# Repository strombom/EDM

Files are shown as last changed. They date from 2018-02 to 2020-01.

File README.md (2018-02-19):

# EDM

## Control board
* Stepper motor output.
* Power board control output.
* Buttons for stepper motor up/down and EDM start/stop.
* LCD display 4x20 characters for status.
* Potentiometers for setting voltage, current (not implemented in this revision), on-time and off-time.

## Power board
* Voltage source, low current for initiating spark. Selectable 250 V, 200 V, 150 V or 100 V. Status comparator checks if voltage is above 70 V.
* Current source, for providing current to the spark. Current limited to 10 A, adjustable with potentiometer.
Spark output, has two power transistors to enable the control board to control the voltage and current outputs independently. Has two comparators (5 V and 30 V) to give feedback to the control board, monitoring if a spark has started (breakdown) and to check for short circuit.

## Design files
* [Control Board Schematics](https://github.com/strombom/EDM/raw/master/hardware/edm_control_board/documents/edm_control_board_schematics.pdf)
* [Power Board Schematics](https://github.com/strombom/EDM/raw/master/hardware/edm_power_board/documents/edm_power_board_schematics.pdf)

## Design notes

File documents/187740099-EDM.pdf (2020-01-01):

Anand Pandey et. al. / International Journal of Engineering Science and Technology Vol. 2(6), 2010, 2172-2191

# Current research trends in variants of Electrical Discharge Machining: A review

Anand Pandey¹
Assistant Professor, Department of Mechanical Engineering, Anand Engineering College, Agra –India Email: pandeyanand223@gmail.com

Shankar Singh²
Associate Professor, Department of Mechanical Engineering, SLIET (Deemed-to-be-University), Longowal-India Email:singh.shankar@gmail.com

Abstract

Present manufacturing industries are facing challenges from these advanced materials viz. super alloys, ceramics, and composites, that are hard and difficult to machine, requiring high precision, surface quality which increases machining cost. To meet these challenges, non-conventional machining processes are being employed to achieve higher metal removal rate, better surface finish and greater dimensional accuracy, with less tool wear. Electric Discharge Machining (EDM), a non-conventional process, has a wide applications in automotive, defense, aerospace and micro systems industries plays an excellent role in the development of least cost products with more reliable quality assurance. Die sinking EDM, Rotating pin electrode (RPE), Wire electrical discharge machining (WEDM), Micro- EDM, Dry EDM, Rotary disk electrode electrical discharge machining (RDE-EDM) are some of the variants methods of EDM.
The present paper review the state of the art technology of high-performance machining of advanced materials using Die Sinking EDM, WEDM, Micro-EDM, Dry EDM AND RDE-EDM. The review relies on notable academic publications and recent conference proceedings.

Keywords: EDM; RDE-EDM, RPE; WEDM, Micro-EDM

### 1. Introduction

The advanced materials have attractive properties i.e., high strength, high bending stiffness, good damping capacity, low thermal expansion, better fatigue characteristics which make them potential material for modern day industrial application. Present manufacturing industries are facing challenges from these advanced materials viz. super alloys, ceramics, and composites, that are hard and difficult to machine, requiring high precision, surface quality which increases machining cost [1]. To meet these challenges new processes with advanced methodology and tooling needs to be developed. The conventional machining of such advanced materials are often difficult due to the improved thermal, chemical and mechanical properties of new advanced materials. Conventional machining such as turning, milling and drilling etc shows ineffectiveness in machining of advanced materials, since it results in poor materials removal rate, excessive tool wear and increased surface roughness. Non-Conventional Machining processes are classified according to the type of energy used for the machining of the work materials. i.e. Mechanical (Ultrasonic machining(USM), Water jet machining(WJM),Abrasive jet machining (AJM), Thermal Electrical discharge machining(EDM),Electron beam machining(EBM),Laser beam machining(LBM), and Chemical (Chemical machining(CHM),Photo chemical machining(PCM) [2]. The Electric Discharge Machining (EDM), a thermal material removal process, has firmly established its use in the production of forming tools, dies, molds and effectively machining of advanced materials.

ISSN: 0975-5462 | 2172

### 1.1 Overview of EDM

In Electrical Discharge Machining the electrode is moved downward toward the work material until the spark gap (the nearest distance between both electrodes) small enough so that the impressed voltage is great enough to ionize the dielectric [3]. Short duration discharges (measured in microseconds) are generated in a liquid dielectric gap, which separates tool and work piece. The material in the form of debris is removed with the erosive effect of the electrical discharges from tool and work piece [4]. EDM does not make direct contact between the electrode and the work piece where it can eliminate mechanical stresses chatter and vibration problems during machining [5].

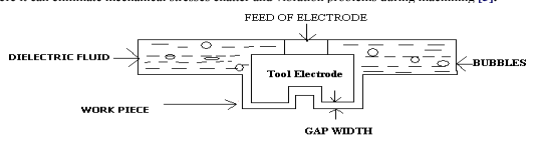
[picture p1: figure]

Fig.1.0 Schematic diagram of EDM

EDM is a non-traditional process based on removing unwanted material in the form of debris from a part by means of a series of recurring electrical discharges (created by electric pulse generators in micro seconds) between a tool called electrode and the work material in the presence of a dielectric fluid( kerosene, distilled water) . The history of EDM begins in 1943, with the invention of its principle by Russian scientists Boris and Natalya Lazarenko in Moscow. They were assigned by the Soviet government to investigate the wear caused by sparking between tungsten electrical contacts, a problem which was particularly critical for maintenance of automotive engines during the Second World War. Putting the electrodes in oil, researchers found that the sparks were more uniform and predictable than in air. They had then the idea to reverse the phenomenon, and to use controlled sparking as an erosion method [6].Lazarenkos developed during the war the first EDM machines, which were very useful to erode hard metals such as tungsten or tungsten carbide. In the 1950’s, progress was made on understanding the erosion phenomenon [7-9]. It is also during this period that industries produced the first EDM machines. Due to the poor quality of electronic components, the performances of the machines were limited at this time. In the 1960’s, the development of the semi-conductor industry permitted considerable improvements in EDM machines. Die-sinking machines became reliable and produced surfaces with controlled quality, whereas wire-cutting machines were still at their very beginning. During the following decades, efforts were principally made in generator design, process automatization, servo-control and robotics. Applications in micro-machining became also of interest during the 1980’s [10]. It is also from this period that the world market of EDM began to increase strongly, and that specific applied EDM research took over basic EDM research [11]. Finally, new methods for EDM process control arose in the 1990’s by using fuzzy control, neural networks response surface methodology, Taguchi optimization.etc.

### 2. Electrical Discharge Machining (EDM)

This section provides the basic fundamentals of the EDM Process and the variations of process combining other material removal methods:

### 2.1 EDM: How it works

The material erosion mechanism primarily makes use of electrical energy and turns it into thermal energy through a series of discrete electrical discharges occurring between the electrode and work piece immersed in a dielectric liquid medium [12]. The thermal energy generates a channel of plasma between the cathode and anode [13] at a temperature in the range of 8000 to 12,000 °C [14]. When the pulsating direct current supply occurring at the rate of approximately 15,000–30,000 Hz [15] is turned off, the plasma channel breaks down. This causes a sudden reduction in the temperature allowing the circulating dielectric fluid to implore the plasma channel and flush the molten material from the pole surfaces in the form of microscopic debris.

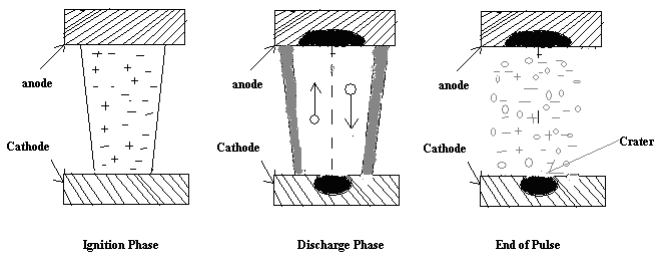
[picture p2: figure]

Fig.2.0 The phases of EDM (Konig and klocke, 1997)

Mc Geough [16] describes the variation of voltage pulses causing the electrical breakdown of the dielectric fluid. A high voltage current is needed to discharge in order to overcome the dielectric breakdown strength of the small gap. The breakdown of this plasma channel occurs because of the acceleration of electrons towards the anode. Electrons impacts with the neutral atoms and molecule of dielectric fluid, thus creating more positive ions and electrons, which accelerated towards the cathode and anode. The impact of these electrons and positive ions to the anode and cathode produces heat energy.
Electrical Discharge occurs at higher frequencies since the metal removal rate for each discharge is very less in change in weight. For every pulse, electrical discharge occurs at a particular position where the electrode materials are melted and evaporated and finally ejected in the molten phase (in the form of debris) thus forming small crater on both tool electrode and work piece. The unwanted material is then cooled and re-solidified in the dielectric fluid forming large number of debris particles which will be flushed away from the gap by the flow of dielectric pressure. During each end of the discharge duration, the temperature of the plasma channel and the electrode surfaces that is in contact of the plasma rapidly drops, resulting in the recombination of ions and electrons. For maintaining stability in EDM process, every successive next pulse discharge occurs at a spot distanced sufficiently far from the previous discharge position. The pulse interval (known as off time period) for the next discharge pulse should be not so much long and not too short .If it is long then the plasma channel that is generated by the previous discharge can be fully de-ionized and the dielectric breakdown strength around the previous discharge location can be recovered by the time the next voltage charge is applied and short pulse interval time produces more surface roughness and instability in machining [17].

### 2.2 EDM Equipments

Electrical discharge machining unit consist of following components:
2.2.1 EDM Circuits

EDM Circuits helps to convert electrical energy into thermal energy and maintain the machining gap (known as spark gap) to generate succession of uniform electrical discharges in the form of sparks. A capacitor is used in the circuits to store electrical energy before discharging each sparks [18].In EDM the most commonly used power supply circuits in EDM process are Resistance –Capacitance (R-C) Circuit, Rotary Impulse Generator Circuit and Controlled Pulse Circuit. RC types of generators are simple and low in cost. It uses resistance and a condenser to generate a nearly a saw tooth voltage waveform. In R-C circuit the condenser of capacitance c is charged through a resistance Rc from a source of current of potential and the charging is continued until the potential of the condenser reaches the breakdown voltage Vc of the gap between the tool and the workpiece.The gap is filled with dielectric fluid. The spark discharge is initiated causing an oscillatory flow of current which reaches a maximum value shortly after the breakdown of the dielectric [19]. Rotary-impulse generator circuit is simply a motor generator set. This type of generator supplies high voltage in excess of 110v. Arcing is frequent since the voltage waveform is uncontrollable, so the tool wear rate is high. In pulse circuit , vacuum tubes or transistors are used to achieve the pulsing switch effect.Resistence can also be provided in these circuits to slow down the time required for charging the capacitor.

2.2.2 Dielectric Unit:

The dielectric unit systems consist of dielectric tank, a pumping unit and a filtering unit to handle types of dielectric. Dielectric is often used when considering the effect of alternating electric fields on the substance. Mineral oil, kerosene and deionized water are generally used as a dielectric fluid in EDM .The Sinker EDM process uses dielectric acts as a medium through which controlled electrical discharge occours.This dielectric also acts as a quenching medium to cool and solidify the gaseous EDM debris resulting from the discharge [20].

2.2.3 Servo feed control:

Servo head is incorporated in EDM to maintain gap voltage since the dielectric parameters constantly fluctuate. Servo mechanism affecting the movement of the electrode may be either electric motor driven, solenoid operated or hydraulically operated or a combination of these. The servo feed control maintain the working gap at proper width [21].

### 2.3 EDM Process Parameters

This section discusses the process parameters of EDM. This section focuses on the effects of process parameters such as electrical and non-electrical parameters on the various performance measures.

2.3.1 Electrical Parameters

- Pulse Duration (Ton): It is the duration of time measured in micro seconds. During this time period the current is allowed to through the electrode towards the work material within a short gap known as spark gap. Metal removal is directly proportional to the amount of energy applied during the on time period [22]. Pulse duration is also known as pulse on time and the sparks are generated at certain frequency. Material removal rate depends on longer or shorter pulse on time period. Longer pulse duration improves removal rate of debris from the machined area which also effects on the wear behavior of electrode. As in EDM process erosion takes place in the form of melting and vaporization of both the tool and work material at the same time period, so with longer pulse duration more material has to be melt and vaporize. The resulting crater produced will be broader as comparison to the shorter pulse on time. But, in some experimental research work it has been proved that optimal pulse duration gives higher performance measures [23]. It conclude all that MRR can not be increased by increasing the Pulse on time, a suitable combination of peak current is also needed for increasing rate of removing unwanted material from the work piece. At constant current and constant duty factor, the MRR is decreased with increase in pulse on time [24]. This is due to the reason because of short pulses cause less vaporization, where as long pulse duration causes the plasma channel to expand rapidly. This expansion of plasma channel cause less energy density on the work material, which is not sufficient to melt and vaporize the work material. It was also concluded by the researchers that with increase of pulse duration, surface roughness decreased, hardness of work material, crack length, crack width and the thickness of recast layer increased.

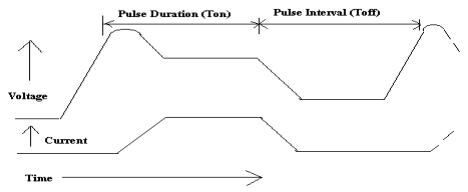
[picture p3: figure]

Fig.3.0 Actual profile of single EDM pulse (Fuller, 1996)

- Pulse Interval (Toff):

It is the waiting interval time period during two pulses on time periods. In fig.1.7, it is the duration of time in which no machining takes place (idle time period) and it allows the melt material to vaporize and to remove from setting. This parameter is to affect the speed and the stability of the cut. If the off-time is too short, it improves MRR but it will because more sparks to be unstable in the machining zone .Kansal et al.
[25] result out that increase in pulse interval time decreases the MRR. Saha et al. [26] reported out that for small value of pulse interval time period, the MRR was low, but with further increase MRR increases. MRR was dropped slowly with increase in pulse interval time. This is due to very short pulse interval the probability of arcing is larger because dielectric in the gap does not recover its dielectric strength. O.A. Abu Zeid investigated the role of voltage, pulse off time in the electro discharge machined AISI T1 high speed steel [27]. The researcher concluded that the MRR is not so much sensitive to pulse interval time changes at low pulse on time in finish machining.

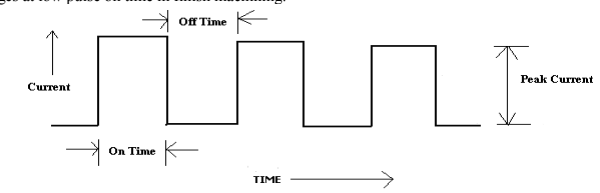
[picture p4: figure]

Fig.4.0 Pulse wave form of pulse generator [28]
- Electrode gap (spark gap):
It is the distance between the electrode and the part during the process of EDM. An electro-mechanical and hydraulic systems are used to respond to average gap voltage. To obtain good performance and gap stability a suitable gap should be maintained. For the reaction speed, it must obtain a high speed so that it can respond to short circuits or even open gap circuits. Gap width is not measured directly, but can be inferred from the average gap voltage [28].

### 2.3.2 EDM Research

Electrical discharge machining is one of the profitable machining processes used for accurate and high precision geometry of the work piece. EDM can become more reliable by doing the research on performances to be obtained by it. Some of the research areas in EDM are shown in fig.5.0

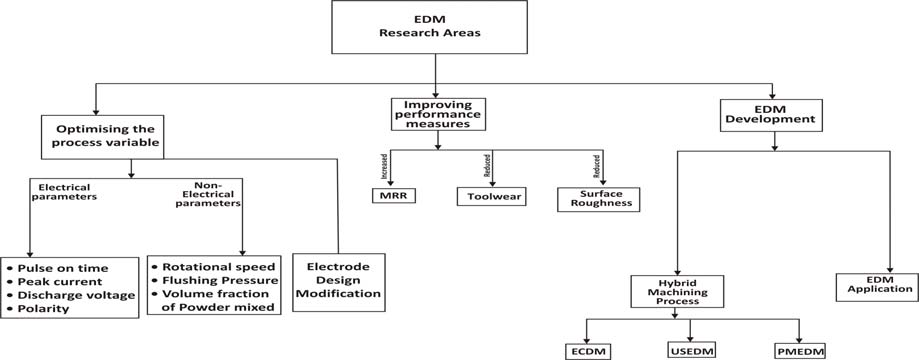
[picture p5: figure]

Fig.5.0 Classification of EDM research

- Duty cycle:
It is a percentage of the on-time relative to the total cycle time. This parameter is calculated by dividing the on-time by the total cycle time (on-time plus off-time).It indicates the degree of efficiency of the operation.

F.L.Amarim result out the effect of duty cycle on the machining of AMP-8000. The researchers concluded that increase of duty factor increases MRR. This is due to the reason that with increase of duty cycle a black layer was seen on the surface of work material and with further more increase of it, the machining becomes unstable [29].MRR increases with increase in duty factor at constant current constant pulse on time [24].This is due to the reason that with increase in duty cycle, the intensity of spark increases resulting in higher MRR.

- Polarity:
It may be positive or negative connected to tool electrode or work material. Polarity can affect processing speed, finish, wear and stability of the EDM operation. It has been proved that MRR is more when the tool electrodes are connected at positive polarity(+) than at negative terminal( -) .This may be due to transfer of energy during the charging process is more in this condition of machining. When a electrical discharge is generated electrons dispatch from the negative polarity collides with neutral molecules between the work piece and electrode which is responsible for ionization process in EDM. However, ionization is taken because the electron arrives at the positive terminal of the surface. The negative polarity is more desirable as compared to positive polarity [30]. The researcher concluded this is because the MRR is higher and better surface finish is produced as MRR is dependent on anode potential drop. Chow et al. experimentally work on the micro slitting on titanium alloy with copper as rotating disk as a electrode. They concluded that MRR was lower with positive polarity of work piece as compared to negative polarity. This is due to the fact that with positive polarity of work piece, the dissociated carbon elements in the dielectric fluid tend to adhere to the anode, which result in forming a recast layer [31].

### 2.4. Non Electrical Parameters

Non-electrical parameters such as the Rotational movement of electrode, flushing of dielectric fluid and aspect ratio ( tool shape) together play a significant role in delivering optimal performance measures. This section discusses the effects of non-electrical parameters on the various performance measures.

2.4.1 Rotation of Tool Electrode:

It is the rotational effect of cylindrical (pin shaped) or disc shaped electrode tool measured in revolution/minute. The rotational movement of electrode is normal to the work surface and with increasing the speed, a centrifugal force is generated causes more debris to remove faster from the machining zone. According to Mohan et al. [23], the centrifugal force generated throws a layer of dielectric in to the machining gap, induces an atmosphere for better surface finish, prevent arching and improves MRR. Soni and Chakraverti [32] compared the various performance measures of rotating electrode with the stationary electrode. The results concluded an improvement in MRR due to the better flushing action and sparking efficiency with little tool wear but the surface finish was improved.

2.4.2 Injection flushing:

Flushing removes eroded particles from the gap for efficient cutting and improved surface finish of machined material. Flushing also enables fresh dielectric oil flow into the gap and cools both the electrode and the work piece. Basic characteristics required for dielectric used in EDM are high dielectric strength and quick recovery after breakdown [33].There variations of EDM processes can be classified according to the type of dielectric fluid used. Most dielectric media are hydrocarbon compounds and water. The hydrocarbon compounds are in the form of refined oil; better known as kerosene. While the fluid properties are essential, the correct fluid circulating methodology is also important. The dielectric fluid not only forms a dielectric barrier for the spark between the work piece and the electrode but also cools the eroded particles between the work piece and the electrode. The pressurized fluid flushes out the eroded gap particles and remove the debris from the fluid medium by causing the fluid to pass through a filter system [34].During the investigation of EDM of Ti 6Al 4V, Chen et al. [35] found that the MRR was greater and the relative EWR is lower, when using 16 distilled water as dielectric solution.

2.4.3 Tool Geometry:

Tool geometry is concerned with the shape of the tool electrodes.ie. Square, rectangle, cylindrical, circular.etc. The ratio of length /diameter of any shaped feature of material. In case of rotating disk electrode the ratio becomes thickness/diameter. Murali et al [36] used graphite foil for straight grooving operation instead of pin shaped electrode. An aspect ratio of 2.3 was achieved by using FAST technique (Foil as tool electrode) which was improved to 8 by implementing GAME (Gravity assisted Micro EDM). Singh et al. [37] uses square and rectangular shaped electrodes having aspect ratio of 1.0 and 0.6 for machining 6061Al/Al2O3P composite .It concluded that shape of the electrode effects EWR. The tool having less aspect ratio gave higher value of EWR.Thus with increasing the size of electrode more good performance of ED Machining takes place.

2.4.4 Tool Material (Electrode):

Engineering materials having higher thermal conductivity and melting point are used as a tool material for EDM process of machining . Copper, graphite, copper-tungsten, silver tungsten, copper graphite and brass are used as a tool material (electrode) in EDM. They all have good wear characteristics, better conductivity, and better sparking conditions for machining. Copper with 5% tellurium, added for better machining properties. Tungsten resist wear better than copper and brass .Brass ensures stable sparking conditions and is normally used for specialized applications such as drilling of small holes where the high electrode wear is acceptable (Metals Handbook, 1989). The factors that effect selection of electrode material include metal removal rate, wear resistance, desired surface finish, cost of electrode material manufacture and material and characteristics of work material to be machined.

### 2.5 Recast Layer in EDM:

In EDM process as the sparks are generated the material begins to melt and vaporize with small crater, thus reducing the area of work piece material into gas bubbles. During the each cycle period EDMed crater gets larger, its increasing surface area begins to sink heat away from the spark gap until the vaporization temperature can no longer be sustained. The melting process continue but an pulse interval time period is required to flush away the eroded material .During the off time period when the current is switched off, melting ceases instantly and all molten material break away in the form of small spherical bubbles is drawn back by the surface tension and resolidifies back on to the cooler layer of cut material. This thin layer of resolidified material is called recast layer or white layer [38]. Immediately below the recast layer is the area termed as heat affected zone (HAZ). This area is partially affected by the elevated temperature of the spark gap. Within this area, the material did not approach temperature large to melt, but reaches a temperature high to change its temper, reducing its hardness. While machining the maraging steel with EDM process a recast layer was formed [24]. These results in premature part failure and shorten the life of part’s fine surface finish.

Fig.6.0 EDM heat effected Zones [41]

Pandey et al. [39] reported out that the thickness of the recast layer formed on the work piece and the level of
thermal damage | suffered | by the electrode can be determined by analyzing the growth of the plasma
channel during sparking. The EDM generates heat affected zone in the machining zone [40]. The researchers measured the micro hardness around the micro- EDMed hole crossections. They concluded that HAZ in micro EDM comprises of low hardness instead of white layer.

### 3.0 EDM Variants

In die sinking process the tool electrode is the replica of the machined profile of the work material shown in fig 7.0 Die sinking process solves the problem of manufacturing accurate and complex-shaped electrodes of three-dimensional cavities. According to the article “Advancing EDM through Fundamental Insight into the Process” by M. Kunieda Tokyo University of Agriculture and Technology, Japan), B. Lauwers (Katholieke Universities Leuven, Belgium), K.P. Rajukar (University of Nebraska-Lincoln, USA), B.M Schumacher (University of Applied Science St Gallen, Switzerland),the work piece can be formed either by replication of a shaped tool electrode or by 3-Dimensional movement of a simple electrode similar to milling or we can use the combination of both the methods.

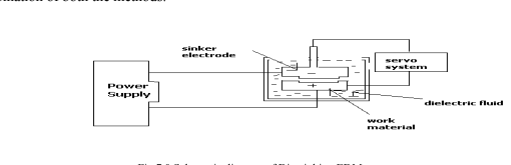
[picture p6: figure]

Fig.7.0 Schematic diagram of Die-sinking EDM
A number of EDM variations based on this basic configuration have emerged in the industry to cope with the machining of smart materials or super alloys used exclusively in the manufacture of aeronautical and aerospace parts. Wire-cut EDM (WEDM) and Rotary Disk electrode electrical discharge machining process (RDE-EDM) are some of the most favorable variants owing to its ability to machine conductive, exotic and high strength and temperature resistive (HSTR) materials with the scope of generating intricate shapes and profiles [41].

### 3.1 Wire EDM process:

WEDM was first introduced to the manufacturing industry in the late 1960s. In WEDM, material is eroded from the work material by a series of discrete sparks occurring between the work piece and the wire separated by a stream of dielectric fluid, which is continuously fed to the machining zone [42]. The WEDM process makes use of electrical energy generating a channel of plasma between the cathode and anode [43], and turns it into thermal energy at a temperature in the range of 8000–12,000 ºC [44]. When the pulsating direct current power supply occurring between 20,000 and 30,000 Hz [45] is turned off, the plasma channel breaks down. This causes a sudden reduction in the temperature allowing the circulating dielectric fluid to implore the plasma channel and flush the molten particles from the pole surfaces in the form of microscopic debris.

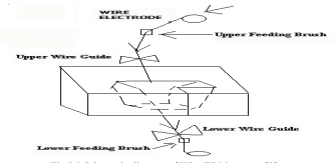
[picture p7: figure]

Fig.8.0 Schematic diagram of Wire EDM process [2]

3.1.1 WEDM process monitoring and control of smart material

Lok et al. [46] presented the finding of processing two advanced materials Sialon and Al2O3-TiC by using WEDM. The author has taken MRR and surface finish as output parameters. The surface damage was evaluated by flexural strength data. The variability of flexural strength data was analyzed by weibull stastical method. The mean flexural strength drops from 32% to 67% due to thermal spalling erosion mechanism of wire-cut EDM process. Yan et al. [47] machined aluminum matrix composites (Al2O3p/6061 Al) using WEDM. The effect of pulse on time, cutting speed, width of slit, surface roughness was studied. The wire easily got broken while machining Al2O3p/6061 Al. It was observed that that the cutting speed, surface roughness and width of the slit significantly depend upon volume fraction of Al2O3 particles. Less volume percentage of reinforcement increases the surface finish, improves width of slit.
Hascaly et al. [48] performed an experiment for finding out the machining characteristics of AISI D5 tool steel in WEDM. The author concluded that intensity of process energy affect the surface roughness as well as micro cracking. The wire speed and fluid pressure do not have much influence. Gokler et al. [49] performed experiments to optimize the cutting and offset parameter combination for WEDM process to achieve the desired surface roughness. The author has performed experiments on 1040 steel material of thickness 30, 60 and 80 mm and on 2379 and 2378 steel materials of thickness 30 and 60 mm. It was concluded that increase in the work piece thickness creates better surface roughness characteristic.Tarng et al. [50] used a neural network system to determine settings of pulse duration, pulse interval, peak current, open circuit voltage, servo reference voltage, electric capacitance, and table speed for the estimation of cutting speed and surface finish.

3.1.2 Wire breakage in EDM

A wide variety of the control strategies preventing the wire from breaking are built on the knowledge of the characteristics of wire breakage .Saha et al. [51] developed a model that predicts the thermal distribution accurately, increase wire velocity and reduction in heat transfer coefficient. He has found that non uniform heating is the most important variable affecting the temperature stress. FE Model would help to prevent wire breakage. Tosun et al. [52] found that increasing pulse duration and open circuit voltage increase the wire wear rate, whereas the increasing wire speed and dielectric fluid pressure decreases the wire wear. Luo et al. [53] claimed that the wire material yielding and fracture contribute to the wire breakage, whilst an increase in temperature aggravates the failure process.

3.1.3 Modeling of WEDM process

Tarng et al. [50] formulated a neural network model and simulated annealing algorithm in order to predict and optimize the surface roughness and cutting velocity of the WEDM process when machining of SUS-304 stainless steel materials. T.A. Spedding and Z.Q.Wang [54] attempted to model the cutting speed and surface roughness of WEDM process through the response-surface methodology and artificial neural networks (ANNs) and have found that the model accuracy of both the approaches were better. The same authors (T.A. Spedding and Z.G. Wang, 1997) attempted further to optimize the surface roughness, surface waviness and speed of the artificial neural networks that predicted values using a constrained optimization model. Lin et al. [55] proposed a control strategy based on fuzzy logic to improve the machining accuracy. Huang and Liao [56] presented the use of Grey relational and S/N ratio analyses, for determining the optimal parameters setting of WEDM process. The results showed that the MRR and surface roughness are easily influenced by the table feed rate and pulse on time.

### 3.2 MICRO EDM

According to CIRP committee of Physical and Chemical processes, the term micro-machining defines the processes that manufacture products in the range of 1 to 999 μm [57]. Initially, the term was used to present the miniaturization of electronic components and devices. However, with the present trend in the miniaturization of mechanical components, it is also being applied for the generation of microscopic mechanical components and devices[28].In order to reduce the size of product micro-edm was developed and the basic physical characteristics of the micro-EDM process is essentially similar to that of the conventional EDM process with the main difference being in the size of the tool(electrode) used, the power supply of current and voltage supply , and the resolution of the X-, Y- and Z- axes movement. The system has a servo system with highest sensitivity and positional accuracy of + 0.5 μm [58].It permits setting of a minimized discharge gap width of 1 μm [59]. There fore, the system is helpful for conventional precision engineering purposes as well as for micro-components fabrication like micro-molds, micro inserts, and in general filigree structure up to 5 μm [58].
Yan et al. [60] investigated effects of various machining parameters on the quality of the micro-hole machining of carbide by EDM. Fuel injector valves, parts and components for medical devices, fiber optic connectors, micromachining, micro-mold making, stamping tools, and micro electronic parts are the examples of miniaturized and smaller size parts produced by the micro-EDM technology. . Zhang et al. [61] made an experiment in hole machining of Al2O3 ceramics with small diameter and metal bond diamond wheels after micro electric discharge truing to investigate its effectiveness.
Wansheng et al. [62] demonstrated that holes with diameter less than 0.2 mm and the aspect ratio more than 15 can be produced without difficulty by ultrasonic vibration using micro-EDM .Kaminski and Capuano [63] reported that they studied parameters affecting the micro-hole machining process with diameters smaller than 0.1 mm and aspect ratio bigger than 20 by electro erosion penetration process in sheets. Diver et al. [64] investigated the possibility of a novel technique to produce reverse tapered micro-holes using EDM. High quality reverse tapered holes are claimed to be produced, showing excellent hole form, with hole diameter variation around 3 μm and cycle times similar to standard EDM for straight holes. The quality of hole surface finish maintained at Ra=0.3 μm. Liu et al. [65] investigated the feasibility of fabricating high nickel alloy using micro-EDM, and micro-holes were successfully fabricated in high nickel alloy. Liu et al. [66] studied micro-EDM combined with High-Frequency Dither Grinding (HFDG) to improve the surface roughness of micro-holes, reducing from 2.12 μm to 0.85 μm without micro cracks.

### 3.3 DRY EDM:

Dry EDM uses gas-liquid mixture as the two phase dielectric fluid and has the advantage the concentration of liquid and properties of dielectric fluid to meet desired performance responses. In dry EDM, tool electrode is formed to be thin walled pipe. Dry EDM uses gas as dielectric fluid, and high MRR can be obtained to cut high strength engineering materials with the presence of oxygen [67–70].High-pressure gas or air is supplied through the pipe. The role of the gas is to remove the debris from the gap and to cool the inter electrode gap. The technique was developed to decrease the pollution caused by the use of liquid dielectric which leads to production of vapour during machining and the cost to manage the waste. V.Ramani et al. [71] reported that helium and argon can be used as a dielectric medium to drill holes using copper electrodes. Later on Kunieda et al. [72] confirm that by introducing oxygen gas into the discharge gap increases the material removal rate in water as a dielectric medium. Tao et al. [73] concluded that by combining oxygen gas with copper tool gives high MRR in dry EDM. Dry EDM with air as the dielectric is feasible with reverse polarity [26].

### 3.4 Rotating Disk Electrode(RDE)-EDM:

Machining by using Rotary Disk Electrode is a typical method of EDM, which develops in recent years. In recent years the studying of micro electro mechanical Systems (MEMS) have resulted in the manufacture of small size products such as micro-pumps, micro-engines and micro-robots that have been successfully used in industrial applications. The technique of precision machining for such small devices has become increasingly important [74–77]. Rotary disc electrode electrical discharge machining is one of the variant process of electrical discharge machining process based on removing unwanted material in the form of debris from a part by means of a series of recurring electrical discharges (created by electric pulse generators in micro seconds)between a rotary tool called disc( thickness ranging from micron level to 1 mm) and the work material in the presence of a dielectric fluid( kerosene, distilled water ). This fluid makes it possible to flush eroded particles from the gap.
This new application of RDE-EDM machining is achieved by locating the rotating disk Electrode above or below the work piece to improve the debris removal rate.

### 3.4.1 Past work done on RDE-EDM:

A significant number of papers have been reviewed on ways of yielding optimal performance measures of high MRR, low tool wear rate (TWR) and satisfactory surface quality. This section will review all the past research work done in rotary EDM for machining advanced materials.
Several researchers have explained the material removal mechanism in terms of migration of material elements between the rotary disk electrode (RDE) and work piece. The material removal takes place not only by vapour ejection but also due to liquid expulsion. Sato et al. [78] developed an electrical discharge machine for micro-hole boring. They claimed that electrode rotation served as an effective gap flushing technique, yielding better material removal.
Soni & Chakraverti [32] introduced rotary disc for grooving operation on titanium alloy. The rotary electrode was placed above the work material. The difficulty of debris problem was encountered the research work i.e. lower metal removal rate and arching occurs due to the accumulation of debris particle between the electrode and work piece.
Soni et al. [79] experimented the machining of die steel and titanium alloy with a rotary and low vibrating copper-tungsten electrode revealed that electrode rotation improves the material removal rate. They also studied the alloying effect of migrating material from electrode and work material. During the research it was observed that performance measures between rotary and stationary electrodes revealed improvement in material removal due to better flushing action and sparking efficiency with low electrode wear during rotary electrical discharge machining. Soni et al. [80] uses copper-tungsten electrode for blind and through hole operation on high carbon high chromium die steel and titanium alloy. It was found that metal removal rate was increased due to rotating electrode which increases the flushing action. Material removal rate was more in case of die steel than titanium allow due to its lower specific strength and less hardness.

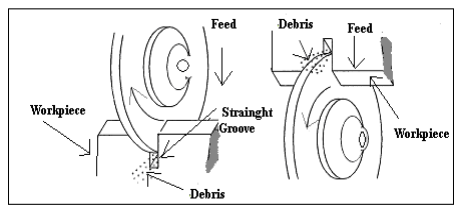
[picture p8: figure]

Fig.9.0 Rotating Disk Electrode Schematic Diagram [81]
Chow et al. [81] used rotary electrode in a modified conventional electrical discharge machine for micro slitting of work piece. The research concluded that increase in material removal and uniform decrease in electrode wear around its periphery by locating the work piece above rotary disk electrode. Reduction in recast layer thickness and lesser micro cracks concentration was also observed on the eroded surface. Yan et al. [82] optimized the cutting of Al2O3/6061Al composite using rotary electrical discharge machining with a disk like electrode with Taguchi methodology. Taguchi methodology revealed that, in general electrical parameters ( Peak Current, Pulse duration and gap voltage) affects the machining characteristics(material removal rate, electrode wear rate & surface roughness) more significantly than the non-electrical parameters (speed of rotational disc).High MRR was found due to superior debris disposal effect of RDE.
C.C.Wang et al. [83] optimizes the blind-hole drilling of Al2O3/6061Al composite using rotary electro-discharging machining by using Taguchi methodology. Increase of rotational speed of the electrode or the injection flushing pressure of the dielectric fluid result in a higher MRR. Ghoreishi and Atkinson [84] compared the effects of high and low frequency forced axial vibration of the electrode rotation in EDM. Vibro-rotary increases less material removal rate as compared with vibration EDM alone but improved surface finish .Combination of ultrasonic vibration and rotation of electrode leads to increase in MRR, TWR AND SR. Mohan et al. [85] studied the effect of machining variables on MRR.EWR AND SR by blind hole drilling through cylindrical rotary electrode (copper) and compared its result from stationary electrode .MRR increases with increase in discharge current and for specific current it decreases with increases in pulse duration. MRR decreases with increase in vol. % of Sic but Increases with rotational speed of electrode which results in positive effect with MRR, TWR and better SR than stationary electrode. Mohan et al. [23] studied the effect of machining variables by blind hole drilling through cylindrical tube electrode made of brass, having eccentric hole diameters .MRR increases with increase of discharge currents and MRR, EWR and SR were more with positive polarity of the electrode than at negative.
M.Murali et al. [36] uses a graphite foil for making straight grooves by Foil as tool electrode approach (FAST).The profile made by FAST EDM appears to have a concave shape with raised edges. This was further refined by using the Gravitational assisted micro EDM (GAME) in which work material was placed above the foil electrode for the effective debris removal, which has improved the aspect ratio to about 8.

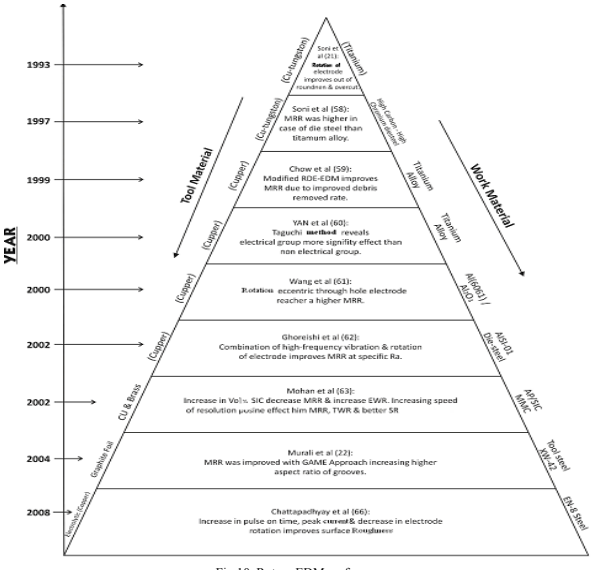
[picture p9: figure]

Fig.10. Rotary EDM performance

Kuo et al. [86] fabricated the micro disk by the application of micro EDM through Wire. The series-pattern micro-disk was used as a rotating tool electrode, which is referred to as micro-rotating disk electrode (MRDE), to simultaneously achieve micro-slits with widths as low as 8 μm. Shih et al. [87] have reported about the electrical discharge grinding of AISI D2 tool steel work piece using a rotary disk copper electrode mounted on horizontal spindle. It was observed that lower electrode wear rate and higher material removal rate can be obtained in this process. Chattopadhyay et al. [88] investigates the machining characteristics of EN-8 steel with copper as a tool electrode during rotary electrical discharge machining process. In the case of MRR and EWR, it has been seen that the decrease in pulse on time, decrease in electrode rotation and increase in peak current, increases both the machining output, while investigation is carried out with rotary electrode.

### 4.0 Hybrid Electrical Discharge Machining Processes

Hybrid machining process in EDM make use of the combined advantages and to reduce some negative effects the combined processes produce better performance as compared to individual process machining. In EDM process the electrical energy is converted to thermal energy, the combined effect of powder suspension and ultrasonic motion of tool or work piece as been reported in this section.

### 4.1 Powder mixed EDM (PMEDM)

EDM process in pure kerosene shows instability resulting to the arcing effect. In order to improve the machining efficiency, the addition of abrasives and metallic powders is done to dielectric fluid. Erden et al. [89] research out the effect of suspended powder particles (Al, Cu, Fe, and carbon) on the mach inability of mild steel. It was observed that the added powder increases the breakdown characteristics of the dielectric fluid, and the machining rate increases with an increase in the concentration of the added powder. It was also observed that the machining becomes Unstable and difficult at an excessive powder concentration due to the occurrence of short-circuiting. Jeswani et al. [90] carried out the research by the addition of fine graphite powder into kerosene oil on the machining of tool steels. It was resulted out that the addition of 4 g/l of graphite powder increases the interspace for electric discharge initiation and lowered the breakdown voltage.

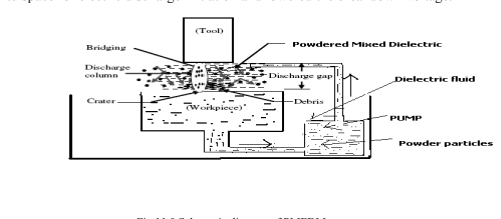
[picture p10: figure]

Fig.11.0 Schematic diagram of PMEDM
Narumiya et al. [91] studied the addition aluminum and graphite powders in dielectric fluid which results in better surface finish than the silicon powder. The best results are obtained for aluminum and graphite powder particles having diameters less than 15 μm and concentration ranges from 2 to 15 g/l. Mohri et al. [92] studied the effect of silicon powder addition into dielectric fluid on the surface finish of H-13 die steel. Machining with addition of silicon powder produces fine and corrosion-resistant surfaces having roughness of 2 μm. Kobayashi et al. [93] investigated the effects of suspended powder in dielectric fluid on surface roughness. It was reported that the surface finish of SKD-61 material is improved with the use of silicon powder. Yan et al. [94] studied the effect of suspended aluminum and silicon carbide powders on EDM of SKD11 and Ti-6Al-4V. Improvement in metal removal rate was observed at the cost of surface finish.
Ming et al. [95] studied out the additives (conductive and inorganic oxide particles) increases the Metal removal rate and decreases the tool wear rate, and improves the surface quality of the work material. Uno et al. [96] investigated the effect of silicon powder mixing on the surface generation mechanism. The EDM with silicon powder mixed fluid produced better surface finish as compared to those produced by EDM with kerosene fluid. It was argued that silicon powder mixed EDM fluid led to smaller undulation of a crater because the impact force acting on the work piece is smaller. This results in the stable machining without a short-circuit between the electrode and the work material. In another study, Uno et al. [97] result out that nickel powder mixed EDM modifies the surface of aluminum bronze components. Nickel powder deposit a layer on an EDM surface to make the surface abrasion-resistant. Wong et al. [98] observed that machining of SKH-54 tool steel in addition of graphite powder particles results in higher material removal rate and better discharge dispersion. Chow et al.
[99] studied the EDM process by adding Sic and aluminum powders into kerosene for the micro- slit machining of titanium alloy. Mixed Sic and aluminum powder to the kerosene enhanced the gap distance, resulting in higher debris removal rate and material removal depth. Pecas et al. [100] result out the effect of silicon powder mixed dielectric on EDM. Improvement in surface finish was assessed through quality surface indicators and process time measurements over a set of different processing areas.

Kansal et al. [101] experimentally studied the effect of addition of silicon powder in dielectric fluid and enhanced rate of material removal and surface finish was achieved. Empirical modelling with response surface methodology concluded the variation of response parameters in terms of independent parameters within the specified range. The silicon powder suspended in the dielectric fluid of EDM affects both MRR and SR. It was found that MRR increases with the increase in the concentration of the silicon powder. Later on Kansal et al.
[25] studied the effect of addition of silicon powder on machining rate of AISI D2 Die Steel. It was found that Peak current, concentration of the silicon powder; pulse-on time, pulse-off time, and gain significantly affect the material removal rate in PMEDM. Chow et al. [102] uses Sic powder in water as dielectric for micro slit operation. They concluded that the addition of Sic powder increases the electrical conductivity, enlarge the inter electrode gap, removes debris easily and increases MRR.Till very few researches has been seen in grooving and slitting machining operation with addition of powder mixed EDM. Kozak et al. [103] have estimated that electrical breakdown in the gap with conducting/non-conducting abrasive powders would be initiated at 3 or 1.5 times larger distance than in case of EDM with pure dielectric fluid, respectively. Extensive studies on the role of abrasives in AEDM have revealed that in hybrid ED process, using abrasive powder, the thermal erosion phenomenon is directly involved in metal removal whereas, the presence of powder assists in improving the machining capabilities by creating a favourable machining environment. Some hybrid processes have also been employed on composites to study their effects. Abrasive powder-mixed EDM or Abrasive EDM (AEDM) was utilised to explore the influences of process parameters. This process requires proper powder suspension and continuous filtration for ensuring even distribution throughout the cavity, facilitating excellent sidewall finishes, thus restricting it to finish machining of component [104].
Later on a comparative machinability study has also been carried out on stir-casted 6061Al/Al2O3p/20p work specimens with copper electrode tools by using plain dielectric fluid and Silicon Carbide (Sic) abrasive powder-suspended dielectric fluid and evaluating the machinability in terms of Surface Roughness (SR). The results of both the processes were analysed using Lenth’s method to find the significant parameters and obtaining optimum machining parameter settings. It was found experimentally that Abrasive Particle Size (APS); Abrasive Particle Concentration (APC) and pulse current are the most significant parameters that affect the
surface characteristics[105]. Singh et al. | analyse the effect of | Abrasive powder-mixed EDM of
6061Al/Al2O3p/20p work specimens with copper tool electrode .They concluded that tool electrode lift time and aspect ratio (shape of the tool electrode) also have considerable effect on the machining performance. Experimental results also indicate that compared with conventional EDM, APM/EDM performance, as regards metal removal rate and surface finish, is much superior. In this study, the MRR in APM/EDM is almost twice that possible with EDM. Similar trend is also noticed for surface finish [106].

### 4.2 Ultrasonic Assisted EDM (USEDM)

The hybrid effect ultrasonic vibration of the electrode with EDM has been undertaken since mid 1980s. Ultrasonic is concerned with the vibratory wave of frequency above 16 Kc/s [107]. Ultrasonic machining combined with Electrical discharge machining can improve material removal rate as high as possible on account of decreasing surface finish. It can be used to machine high strength materials i.e. composites and super alloys. In USEDM process the abrasive slurry is replaced by suitable dielectric fluid (kerosene, distilled water,). The Ultrasonic vibration of tool or work piece in combination with electrical discharges produced by the electrode removes material effectively. The motion of direction of tool is generally normal to the work surface. The vibrating movement of the tool electrode or the work piece improves the slurry circulation and the pumping action, by pushing the debris away and sucking new fresh dielectric and which provides ideal condition for discharges, their efficiency and gives higher removal rate [108].

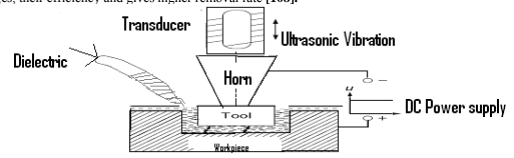
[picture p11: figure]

Fig.12.0 Schematic diagram of USEDM [2]

4.2.1 Tool Vibration in EDM

Murti and Philip (109) added that with the combination of ultrasonic vibration in EDM the MRR and surface finish improved significantly and the tool wear rate increased. Zhixin et al. [110] has produced an ultrasonic vibration pulse electro-discharge machining (UVPEDM) to produce holes in ceramics material. High material removal rate (MRR) was confirmed during the experimental work. Ogawa et al. [111] reported out that the depth of micro holes by the combined effect of EDM with ultrasonic vibration becomes almost two times as that without ultrasonic vibration and machining rate was increased. Yan et al. [112] result out that with combined effect of micro electrical discharge machining (MEDM) and micro ultrasonic vibration machining (MUSM) , the diameter variation between the entrance and exit (DVEE) could obtained about 2 mm in micro holes with diameters of about 150 mm and depth of 500 mm. Ghoreishi and Atkinson [81] compared the effects of high and low frequency forced axial vibration of the electrode, rotation of the electrode and combinations of the methods in respect of MRR, tool wear ratio (TWR) and surface quality in EDM die sinking process. They concluded that vibro-rotary increases MRR by up to 35% compared with vibration EDM and by up to 100% compared with rotary EDM in semi finishing.

4.2.2 Work piece Vibration in EDM

Egashira et al.[113] adopted to vibrate the work piece during machining. Micro holes as small as 5 m in diameter in quartz glass and silicon was machined by EDM with combined effect vibration. In the machining range, high tool wear occurs and sintered diamond tool was used to make machining effective. Prihandana et al.
[114] work out the effect of vibratory work piece. It was result out that work piece vibration increases the flushing effect and high amplitude combined with high frequency increase the MRR. Till less research work has been reported with work piece vibratory motion by EDM process.

### 5.0 Summary

EDM has resulted out as most cost effective and precision machining process in recent years. The capacity of machining hard and difficult to machine parts has made EDM as one of the most important machining processes. The contribution Variants of EDM has brought tremendous improvements in the surface finish of machined advanced engineering materials. Powder mixed EDM and Ultrasonic assisted EDM has not only reduces tool wear but also increases material removal rate. Modeling and optimization of various electrical and non electrical parameters in EDM improved in precision machining of work materials The review of the research trends in EDM on rotary EDM, dry EDM machining, EDM with powder additives, Ultrasonic assisted EDM ,WEDM and Micro EDM performances is presented. In each topic, the development of the methods for the last 50 years is discussed.

References:

1] Kozak, J.; Rajurkar, K.P. (2001): Hybrid machining processes, Evaluation and development, Proceedings of 2nd International Conference on Machining and measurement of sculptured surfaces, Krakow, pp.501-536.

2] Hassan, EI-Hofy. (2005): Advanced Machining Processes, McGraw-Hill, pp. 36-37.

3] Bojorquez, B.; Marloth, R.T.; Es-Said, O.S. (2002): Formation of a crater in the work piece on an electrical discharge machine, Engineering Failure analysis, 9, pp.93–97.

4] Marafona, J.; Chousal, J.A.G. (2005):A finite element model of EDM based on the Joule effect, International Journal of Machine Tools & Manufacture, 46, pp. 1–8.

5] Singh, S.; Maheshwari, S.; Pandey, P.C (2004): Some investigations into the electric discharge machining of hardened tool steel using different electrode materials, Journal of Materials Processing Technology 149, pp. 272–277.

6] Lazarenko, B.R. (1943): About the inversion of metal erosion and methods to fight ravage of electric contacts, WEI-Institute, Moscow in Russian.

7] Germer, L.H.; Haworth, F.E. (1949): Erosion of electrical contacts on make, Journal of Applied physics, 20, 11, pp. 1085– 1109.

8] Cobine, J.D.; Burger, E.E. (1955): Analysis of electrode phenomena in the high-current arc, Journal of Applied Physics, 26, 7, pp.895– 900.

9] Zingerman, A.S. (1956): The effect of thermal conductivity upon the electrical erosion of metals, Souvenir of Physics Technology, pp.11945–1958.

10] Sato, T.; Mizutani, T.; Kawata, K. (1985): Electro-discharge machine for micro hole drilling, National Technical Report, 31, pp. 725– 733.

11] Dauw, D.F.; Van. B. (1995): On the evolution of EDM research, part 2: From fundamental research to applied Research, Proceedings of the 11th International Symposium for Electro Machining (ISEM-11), pp. 133–142.

12] Tsai, H.C.; Yan, B.H.; Huang, F.H (2003):EDM performance of Cr/Cu based composite electrodes, International Journal of Machine Tools & Manufacturing, 43, 3, pp.245–252.

13] Shobert, E.I. (1983): What happens in EDM Electrical Discharge Machining: Tooling, Methods and Applications, Society of Manufacturing Engineers, Dearborn, Michigan, pp.3–4.

14] Boothroyd, G.; Winston, A.K. (1989): Non-conventional machining processes, in Fundamentals of Machining and Machine Tools, Marcel Dekker, Inc, New York, 491.

15] McGeough, J.A. (1988): Electro discharge machining in Advanced Methods of Machining, Chapman & Hall, London, 130.

16] McGeough, J.A. (1988): Advanced Methods of Machining, 1st edition. Chapman and Hall, USA, ISBN 0-412-31970-5.

17] Konig, W.; Klocke, F. (1997): Fertigungsverfahren-3, Abtragen and Generieren, Springer, Berlin.

18] Bawa, H.S. (2004): Manufacturing Process-II, The McGraw Hill Companies, pp.186-187.

19] Shah, A.; Prajapati, V.; Patel, P.; Pandey, A. (2007): Development of Pulsed Power DC Supply for Micro-EDM.

20] Mishra, P.K. (1997): Non Conventional machining, The institution of Engineers-India, pp.106-107.

21] Pandey, P.C.; Shan, H.S. (2003): Modern Machining processes, Tata McGraw Hill, pp.92-93.

22] Singh, S.; Kansal, H.K.; Kumar, P. (2005): Parametric optimization of powder mixed Electrical discharge machining by response surface methodology, Journal of Materials Processing Technology, 169, 3, pp. 427-436.

23] Mohan, B.; Rajadurai, A.; Satyanarayana, K.G. (2004): Electric discharge machining of Al–Sic metal matrix composites using rotary tube electrode”, Journal of Materials Processing Technology, 153–154, pp.978–985.

24] Krishna Mohan Rao, G.; Satyanarayana, S.; Praveen, M.(2008):Influence of machining parameters on electric discharge machining of maraging steels-An experimental investigation, Proceeding of the world congress on Eng., Vol. II.

25] Kansal,H.K.; Singh,S.; Kumar,P.(2007):Effect of Silicon Powder Mixed EDM on Machining Rate of AISI D2 Die Steel, Journal of Manufacturing Processes, Volume9, No.1, pp.13-22.

26] Saha, S.K.; Chaudhary, S.K. (2009): Experimental investigation and empirical modeling of the dry electrical discharge machining process, International Journal of machine tools and manufacturing, vol.49, 297-308.

27] Abu Zied,O.A.(1996): The role of voltage pulse off time in the electro discharge machined AISI T1 high speed steel, Journal of Material process Technology,61,pp.287-291.

28] Crookall, J.R.; Heuvelman, C.J. (1971): Electro-discharge machining-the state of the art”, Annual of the CIRP, 20, pp.113-120.

29] Amorim, F.L.; Weingaertnen, W.L. (2002): Influence of duty factor on the die sinking electrical discharge machining of high-strength aluminum alloy under rough machining, Journal of Braz.soc.Mechanical Sciences, 24,194-199.

30] Lee,S.H.; Li,X.P.(2001):Study of the effect of machining parameters on the machining characteristics in electrical discharge machining of tungsten carbide, Journal of materials processing Technology, 115, pp.344-358.

31] Chow, H.M.; Yan, B.H.; Huang, F.Y. (1999): Micro slit machining using electro-discharge machining with a modified rotary disk electrode (RDE), Journal of Materials Processing Technology, 91, pp. 161–166.

32] Soni,J.S.; Chakraverti,G.(1997):Performance evaluation of rotary EDM by experimental design technique, Defense Science journal, Vol. 47, No.1, pp. 65-73.
33] Wong, Y.S.; Lim, L.C.; Lee, L.C. (1995): Effect of Flushing on Electro Discharge Machined Surface, Journal of Materials Processing Technology’. 48, pp. 299-305.
34] Sommer, C. (2000):Non-traditional machining handbook, First edition, Advance Publishing. Houston.
35] Chen, S.L.; Yan, B.H.; Huang, F.Y. (1999): Influence of kerosene and distilled water as dielectric on electric discharge machining characteristics of Ti 6Al 4V, Journal of Materials Processing Technology, 876, pp. 107-111.
36] Murali, M.; Yeo, S.H. (2004): A novel sparks erosion technique for the fabrication of high aspect ratio micro-grooves, Microsystems Technologies, 10, pp. 628–632.
37] Singh, S.; Maheswari, S.; Pandey, P.C. (2007): Optimization of multiperformance characteristics in electrical discharge machining of Aluminium matrix composites (AMCs) using Taguchi DOE methodology, International Journal of Manufacturing Research, vol.2, No.2, pp.138-163.
38] Guitrau, E. (2008): Recast layer, EDM Today.
39] Pandey, P.C.; Jilani, S.T. (1986): Plasma channel growth and the resolidified layer in EDM, Precision Eng, 8(2), pp.104-110.
40] Thao, O.; Joshi, S.S. (2008): Analysis of heat affected zone in the micro-electro discharge machining, International Journal of Manufacturing Technology and Management, Vol.13, pp.201-213.
41] Hassan, EI-Hofy. (2005): Non tradional and Hybrid machining process, McGraw Hill, pp.158.
42] Puri, A.B.; Bhattacharyya, B. (2003): An analysis and optimization of the geometrical inaccuracy due to wire lag phenomenon in WEDM, International Journal of Machine Tools Manufacturing. 43, 2, pp.151–159.
43] Shobert, E.I. (1983): What happens in EDM, Electrical Discharge Machining: Tooling, Methods and applications, Society of Manufacturing Engineers, Dearbern, Michigan, pp. 3–4.
44] Boothroyd, G.; Winston, A.K. (1989): Non-conventional machining processes, Fundamentals of Machining, Marcel Dekker, Inc, 491. 45] McGeough, J.A. (1988): Electro discharge machining, Advanced Methods of Machining, Chapman & Hall, London, 1988, pp. 130. 46] Lok, Y.K.; Lee, T.C. (1999): Processing of Advanced Ceramics Using the Wire-Cut EDM process, Journal of Materials Processing Technology 63, pp. 839-843.
47] Yan, B.H.; Tsai, H.C.; Huang, F.Y.; Lee, L.C. (2005): Examination of wire electrical discharge machining of Al2O3 p/6061Al composites, International Journal of Machine Tools & Manufacture, 45, pp.251–259.
48] Hascaly,A.; Caydas,U.(2004): Experimental study of wire electrical discharge machining of AISI D5 tool Steel, Journal of Material Processing Technology, 148, pp.362-367.
49] Gokler, M.I.; Ozanozgu, A.M. (2000): Experimental investigation of effects of cutting parameters on surface roughness in the WEDM process, International Journal of Machine Tools and Manufacture 40, pp. 1831-1848.
50] Tarng, Y.S.; Ma, S.C.; Chung, L.K. (1995): Determination of optimal cutting parameters in wire electrical discharge machining, International Journal of Machine Tools Manufacturing, 35, 129, pp.1693–1700.
51] Saha, S.; Pachon, M.; Ghoshal, A.; Schulz, M.J. (2004): Finite Element Modeling and optimization to prevent wire breakage in electro discharge machining, Mechanics Research Communications 31, pp. 451-463.
52] Tosun, N.; Cogun, C. (2003): An investigation on wire wear in WEDM”, Journal of Material Processing Technology 134, pp. 273-278. 53] Luo, Y.F. (1999): Rupture failure and mechanical strength of the electrode wire used in wire EDM, Journal of Material Processing Technology, 94, pp.208–215.
54] Spedding, T.A.; Wang, Z.G. (1997): Parametric optimization and surface characteristic of wire electrical discharge machining process, Precision Engineering 20, pp.5–15.
55] Lin, C.T.; Chung, I.F.; Huang, S.Y. (2001): Improvement of machining accuracy by fuzzy logic at corner parts for wire-EDM, Fuzzy Sets and Systems 122, pp. 499–511.
56] Huang, J.T.; Liao, Y.S. (2003): Application of Grey relational analysis to machining parameter determination of wire electrical discharge machining, International Journal of Production Research 41, pp.1244–1256.
57] Masuzawa, T.; Tonshoff, H.K. (1997):Three-dimensional micromachining by machine tools”, Annuals of the CIRP, 46, 2, pp. 621-628. 58] Koch,O.; Ehrfeld,W.; Michel,F.; Gruber,H.P.(2001): Recent progress in micro-electro discharge machining technology-Part1, Proceeding of the 13th International Symposium for Electro machining ISEM XIII, Bilbao, Spain.
59] Newman, S.T.; Ho, K.H. (2003): The state of the art-Electrical discharge machining, International Journal of Machine Tools and Manufacture, 43(13), pp. 1287-1300.
60] Yan, B.H.; Huang, F.Y.; Chow, H.M.; Tsai, J.Y. (1999): Micro-hole machining of carbide by electric discharge machining, Journal of Materials Processing Technology, 87, pp. 139–145.
61] Zhang, C.; Ohmori, H.; Li, W. (2000): Precision shaping of small diameter wheels using micro electric discharge truing and hole-machining of Al2O3 material, International Journal of Machine Tools & Manufacture, 40, pp. 661–674.
62] Wansherg, Z.; Zhenlog, W.; shichun, D.; Guanxin, C.; Hongyu, W. (2002): Ultrasonic and electric discharge machining to deep and small hole on titanium alloy, Journal of Materials Processing Technology vol.120, and pp.101–106.

63] Kaminski,P.C.; Capuano,M.N.(2003):Micro hole machining by conventional penetration electrical discharge machine, International Journal of Machine Tools & Manufacture, 43, pp. 1143–1149.
64] Diver, Atkinson, J.; Li, J.J.L. (2004): Micro EDM drilling of tapered holes for industrial applications, Journal of Materials Processing Technology, 149, pp. 296–303.
65] Liu, H.S.; Yan, B.H.; F.Y.Huang, F.Y.; Qiu, K.H. (2005): A study on the characterization of high nickel alloy micro-holes using micro-EDM and their application, Journal of Materials Processing Technology, 169, 418–426.
66] Liu, H.S.; Yan, B.H.; Chen, C.L.; Huang, F.Y. (2006): Application of micro-EDM combined with high-frequency dither grinding to micro-hole machining, International Journal of Machine Tools & Manufacture, 46, pp. 80–87.
67] Kunieda, M.; Yoshida, M. (1997): Electrical discharge machining in gas, Annuals of the CIRP 46/1, pp.143– 146.
68] Wang, T.; Kunieda, M. (2003): Dry EDM for finish cut, Key Engineering Materials 259–260, pp.562–566.
69] Kunieda, M.; Miyoshi, Y.; Takaya, T.; Nakajima, N.; Yu, Z.B.; Yoshida, M. (2003): High speed 3D milling by dry EDM, Annuals of the CIRP 52/1, pp. 147–150.
70] Yu,Z.B.; Jun,T.; Kunieda,M.(2004): Dry electrical discharge machining of cemented carbide, Journal of Materials Processing Technology 149/ 1–3, pp. 353–357.
71] Ramani, V.; Cassidenti, M.L. (1985): Inert gas Electrical discharge machining, Nasa Technical brief number NPO 15660.
72] Kunieda,M.; Furuoa,S.; Taniguchi,N.(1991):Improvement of EDM efficiency by supplying oxygen gas into gap,CIRP Annuals, Manufacturing Technology,40,pp.215-218.
73] Tao, J.; Shih, A.J.; Ni, J. (2008): Experimental study of the dry and near dry electrical discharge milling processes, Journal of Manufacturing Science and Engineering, 130.
74] Belhardj, S.; Mimouni, S.; Saidane, A.; Benzohra, M. (2003): Using micro channels to cool microprocessors: a transmission-line matrix study, Micros elects, Journal 34/4, pp.247–253.
75] Park, H.; Pak, J.J.; Son, S.Y.; Lim, G.; Song, I. (2003): Fabrication of a micro channel integrated with inner sensors and the analysis of its laminar flow characteristics, Sensors and Actuators A: Physical, 103/3, pp.317–329.
76] Wu, H.Y.; Cheng, P. (2003): An experimental study of convective heat transfer in silicon micro channels with different surface conditions, International Journal of Heat Mass Transfer, 46/14, pp. 2547–2556.
77] Benavides, G.L.; Bieg, L.F.; Saavedra, M.P.; Bryce, E.A. (2002): High aspect ratio meso-scale parts enabled by wire micro-EDM, Micro system Technology, 8, pp.395–4015.
78] Sato,T.; Mizutani,T.; Yonemouchi,K.; Kawata,K.(1986): The development of an electro discharge machine for micro hole borin, Precision Engineering,8,pp.163–168.
79] Soni, J.S.; Chakraverti, G. (1994): Machining characteristics of titanium with rotary electro-discharge machining. Wear, 171, (1/2), pp.51–58.
80] Soni, J.S.; Chakraverti, G. (1997): Performance evaluation of rotary EDM by experimental design technique, Defense Science journal, Vol. 47, No.1, pp.65-73.
81] Chow, H.M.; Yan, B.H.; Huang, F.Y. (1999): Micro slit machining using electro-discharge machining with a modified rotary disk electrode (RDE), Journal of Materials Processing Technology, 91, pp. 161–166.
82] Yan,B.H.; Wang,C.C.; Liu,W.D.; Huang,F.Y.(2000):Machining Characteristics of Al2O3/6061Al Composite using Rotary EDM with a Disk like Electrode, International Journal of Advance Manufacturing Technology, 16, pp.322–333.
83] Yan, B.H.; Wang, C.C.; Liu, W.D.; Huang, F.Y. (1999): Experimental investigation of the blind-hole drilling of Al2O3/6061Al composite using rotary electro-discharging machining, International Journal of Advance Manufacturing Technology, 1999, 18, pp.372–379.
84] Atkinson,J.; Ghoreishi,A.(2002): Comparative experimental study of machining characteristics in vibratory, rotary and vibro-rotary electro-discharge machining, International Journal of Material processing Technology,120,pp.374-384.
85] Mohan, B.; Rajadurai, A.; Satyanarayana, K.G. (2004): Electric discharge machining of Al–Sic metal matrix composites using rotary tube electrode, Journal of Materials Processing Technology, 153–154, pp.978–985.
86] Kuo,C.L.; Huang,J.D.(2004): Fabrication of series pattern micro disk electrode and its application in machining micro-slit of less than 10 μm, International journal of machine tools and manufacture, 44, pp.545-553.
87] Shih, H.R.; Shu, K.M. (2007): A study of electrical discharge grinding using a rotary disk electrode, International Journal of advance manufacturing technology.
88] Chattopadhyay,K.D.; Verma,S.; Satsangi,P.S.; Sharma,P.S.(2008):Development of empirical model for different process parameters during rotary electrical discharge machining of copper-steel(EN-8) system, Journal of Materials processing technology.
89] Erden, A.; Bilgin,S.(1980): Role of impurities in electric discharge machining, Proceeding of 21st International Machine Tool Design and Research Conference, pp.345-350.
90] Jeswani, M.L. (1981): Effects of the addition of graphite powder to kerosene used as the dielectric fluid in electrical discharge machining. Journal of Wear, Volume 70, pp.133-139.
91] Narumiya,H.; Mohri,N.; Saito,N.; Otake,H.; Tsnekawa,Y.; Takawashi,T.; Kobayashi,K.(1989):EDM by powder suspended working fluid”, Proceeding of 9th ISEM, pp.5-8.

92] Mohri, N.; Saito, N.; Higash, M. (1991): A new process of finish machining on free surface by EDM methods, Annuals of the CIRP, 40, 1, pp.207-210.
93] Kobayashi, K.; Magara, T.; Ozaki, Y.; Yatomi, T.(1992): The present and future Developments of electrical discharge machining, Proceeding of 2nd International Conference on Die and Mould Technology, Singapore, pp.35-47.
94] Yan, B.H.; Chen, S.L. (1993): Effects of dielectric with suspended aluminum powder on EDM, Journal of the Chinese Society of Mechanical Engineers, vol.14, and pp.307-312.
95] Ming, Q.Y.; He, L.Y. (1995): Powder-suspension dielectric fluid for EDM, Journal of Materials Processing Technology, vol.52, pp.44-54.
96] Uno, Y.; Okada, A. (1997): Surface generation mechanism in electrical discharge machining with silicon powder mixed fluid, International Journal of Electro Machining, vol.2, pp.13-18.
97] Uno, Y.; Okada, A.; Hayashi, Y.; Tabuchi, Y. (1988): Surface integrity in EDM of aluminum bronze with nickel powder mixed fluid, Journal of Japanese Society of Electrical Machining Engineers, vol.32, pp. 24-31.
98] Wong, Y.S.; Lim, L.C.; Tee, R.I. (1998): Near mirror finish phenomenon in EDM using powder mixed dielectric, Journal of Materials Processing Technology, Vol.79, pp.30-40.
99] Chow, H.M.; Yan, B.H.; Huang, F.Y.; Hung, J.C. (2000): Study of added powder in kerosene for the micro-slit machining of titanium alloy using electro-discharge machining, Journal of Materials Processing Technology, Vol.101, pp.95-103.
100] Pecas, P.; Henriques, E.A. (2003): Influence of silicon powder mixed dielectric on conventional electrical discharge machining, International Journal of Machine Tools and Manufacture, Vol.43, pp.1465-1471.
101] Kansal, H.K.; Singh, S.; Kumar, P. (2005): Parametric optimization of powder mixed electrical discharge machining by response surface methodology, Journal of Materials Processing Technology, 169, pp.427–436.
102] Chow, H.M.; Yang, L.D.; C.T.Lin, C.T.; Chen, Y.F. (2008): The use of Sic powder in water as dielectric for micro slit EDM machining, Journal of Material Processing Technology, 195, pp.160-170.
103] Kozak ,J.; Rozenek,M.; Dabrowski,L.(2003): Study of electrical discharge machining using powder suspended working media, Proceedings of the Institution Mechanical Engineers Part B, Journal of Engineering Manufacture, Vol. 217, pp.1597–1602. 104]Singh,S.;Maheshwari,S.;Pandey,P.C.(2006):An experimental investigation into abrasive electrical discharge machining (AEDM) of Al2O3particulate reinforced Al-based metal matrix composites, Journal of Mechanical Engineering, Vol. 7, No. 1, pp.13–33.
105] Singh, S.; Maheshwari, S.; Pandey, P.C.; Dey, A.(2008):Effect of Sic Powder Suspended Dielectric Fluid on the Surface Finish of 6061Al/Al2O3P/20p Composites in Electric Discharge Machining, International Journal of Machining and Machinability of Materials (IJMMM) InderScience, 4(2/3), pp. 252-274.
106] Singh,S.; Maheshwari,S.; Dey,A.; Pandey,P.C.(2010): Experimental Results and Analysis for Electrical Discharge Machining (EDM) of Aluminium Metal Matrix Composites with Powder-mixed Dielectric - the Lenth’s Method”, International Journal of Manufacturing Technology & Management (IJMTM), Inderscience, Special issue, Int. J. Manufacturing Technology and Management, Vol. 21, Nos. 1/2.
107] Pandey, P.C.; Shan, H.S (2003): Modern Machining Process, Tata McGraw Hill publishing, pp.7.
108] Kozak, J.; Rajurkar, K.P. (2001): Hybrid machining process evaluation and development, Proceedings of the 2nd International Conference on Machining and Measurement of Sculptured Surfaces, Krakow, pp.501–536.
109] Murti,V.S.; Philip,P.K.(1987): A Comparative Analysis of Machining Characteristics in Ultrasonic Assisted EDM by Response Surface Methodology, International Journal of Product Research, 25, 2, pp.259–272.
110] Zhixin, J. (1995): Study on Mechanical Pulse Electro discharge Machining,” Precision Engineering, 17, 2, pp.89–93.
111] Hitoshi, O.; Teruo, N.; .Iwao, M. (2001): Study of Micro Machining of Metals by EDM with High Frequency Vibration”, Takushima Prefectual Industrial Technology Center.
112] Yan,B.H.; Wang,A.C.; Huang,C.Y.; Huang,F.Y.(2002): Study of precision micro-holes in borosilicate glass using micro EDM combined with micro ultrasonic vibration machining, International Journal of Machine Tools & Manufacture, 42,pp. 1105–1112. 113] Egashira, T. (1999): Micro ultrasonic machining by the application of work piece vibration”, CIRP Annals— Manufacturing Technology, 48, pp. 131–134.
114] Prihandana,G.S.; Hamdi,M.; Wong,Y.S.;Kimiyuki,M.(2006): Effect of vibrated electrode in electrical discharge machining, Proceedings of the First International Conference and Seventh AUN/SEED-Net Field wise Seminar on Manufacturing and Material Processing, Kuala Lumpur, pp. 133–138.

Authors’ Biographies

Anand Pandey is currently Assistant Professor in the Department of Mechanical Engineering at Anand Engineering College-Agra- India. He received his B.E in Industrial & Production Engineering from Guru Ghasidas University, Bilaspur, India in 2002 and his M.Tech in Manufacturing System engineering from Punjab Technical University, Calendar (India) in 2006. Pandey is currently pursuing his Ph.D from S.L.I.E.T (Deemed to be University)-Longowal. He has published more than 12 papers in International & National conference proceedings. His area of research is Conventional & Non conventional machining process & Composite Materials. He is a life member of ISTE (India).

Dr. Shankar Singh is currently Associate Professor at Department of Mechanical Engineering, Sant Longowal Institute of Engineering and Technology (Deemed-to-be-University), Longowal, Dist. Sangrur (Punjab), India. He has been awarded Ph.D in Production Engineering from University of Delhi, Delhi, India in 2007. Earlier, he received his Bachelor in Engineering (Mechanical) Hons. from Aligarh Muslim University, Aligarh (UP) and M. Tech (Production) from Punjab Technical University, Jalandhar (Pb.) in India. His current research interests include Automotive Engg., Non-Conventional Manufacturing Processes such as Electric Discharge Machining (EDM) etc., Hybrid Machining Processes: Abrasive Powder-mixed EDM, Electro-chemical Discharge Machining etc., and Production, Processing, Characterization and Machining of Metal Matrix Composites (MMCs). His name has been included in the Who's Who in the World (9

th
Edition and 25th Anniversary Edition) of ‘Marquis Who's Who in Science and Engineering’ and First Edition of ‘Marquis Who's Who in Asia’. His name also finds place in 'Leading Engineers of the World 2007', published by International Biographical Centre, Cambridge, England. His name has been nominated for inclusion in the ‘2000 Outstanding Scientists 2008/2009’, published in 2009, by International Biographical Centre, Cambridge, England. He has published 45 technical papers in the International Journals and proceedings of International and National conferences.

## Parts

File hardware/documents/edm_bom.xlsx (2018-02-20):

Ref | Qnty | Value | Digikey
BTN1 | 4 | Button black | 401-1152-ND
KNB1 | 4 | Knob black | 1568-1601-ND

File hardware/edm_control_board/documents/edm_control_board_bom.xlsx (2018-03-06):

Ref | Qnty | Value | Digikey | Footprint
C201, C202, C203, C204, C205, C209, C206, C303, C304, C602 | 10 | 100n | 445-1418-1-ND | Capacitor_SMD:C_0805_2012Metric
C207 | 1 | 1u | 587-2910-1-ND | Capacitor_SMD:C_0805_2012Metric
C210, C208 | 2 | 12p | 311-1100-1-ND | Capacitor_SMD:C_0805_2012Metric
C212, C211 | 2 | 2u2 | 311-3425-1-ND | Capacitor_SMD:C_0805_2012Metric
C301, C302 | 2 | 330n | 1276-6813-1-ND | Capacitor_SMD:C_0805_2012Metric
C305, C306, C601 | 3 | 10u | PCE4209CT-ND | Capacitor_SMD:CP_Elec_6.3x5.3
C401 | 1 | 1800p | 490-3479-1-ND | Capacitor_SMD:C_2220_5650Metric
C603 | 1 | 1n | 311-1469-1-ND | Capacitor_SMD:C_0805_2012Metric
D601 | 1 | CDBA140-G | 641-1015-1-ND | Diode_SMD:D_SMA
J401 | 1 | Conn_02x08_Odd_Even | ED10523-ND | Connector_PinHeader_2.54mm:PinHeader_2x08_P2.54mm_Vertical
J402, J404, J403, J406 | 4 | Conn_01x02 | ED1609-ND | TerminalBlock:TerminalBlock_bornier-2_P5.08mm
J405 | 1 | Conn_01x06 | 952-2270-ND | Connector_PinHeader_2.54mm:PinHeader_1x06_P2.54mm_Vertical
Q202, Q203, Q204, Q201 | 4 | BSS214NW | BSS214NWH6327XTSA1 | Package_TO_SOT_SMD:SOT-323_SC-70
Q601 | 1 | DMN3404L-7 | DMN3404LDICT-ND | Package_TO_SOT_SMD:SOT-23
R202, R203, R204, R201, R207, R206 | 6 | 27k | 311-27.0KCRCT-ND | Resistor_SMD:R_0805_2012Metric
R205 | 1 | 20R | 311-20.0CRCT-ND | Resistor_SMD:R_0805_2012Metric
R401 | 1 | 1M | 311-1.00MFRCT-ND | Resistor_SMD:R_1206_3216Metric
R601 | 1 | 4R99 | 311-4.99CRCT-ND | Resistor_SMD:R_0805_2012Metric
RV201 | 1 | 20k | 3214J-203ECT-ND | Potentiometer_SMD:Potentiometer_Bourns_3214J_Horizontal
RV501, RV503, RV502, RV504 | 4 | POT | 987-1278-ND | Potentiometer_THT:Potentiometer_TT_P0915N
SW501, SW503, SW502, SW504 | 4 | SW_Push | 401-1137-ND | Button_Switch_THT:SW_PUSH_CK_PVA1
U301 | 1 | STM32F722RETx | 497-17184-ND | Package_QFP:LQFP-64_10x10mm_P0.5mm
U302 | 1 | R-78E3.3-1.0 | 945-2409-5-ND | Converter_DCDC:Converter_DCDC_RECOM_R-78E-0.5_THT
U303 | 1 | L78L05_SO8 | 497-1182-1-ND | Package_SO:SOIC-8_3.9x4.9mm_P1.27mm
U501 | 1 | NHD-0420H1Z | NHD-0420H1Z-FSW-GBW-33V3-ND | Display:NHD-0420H1Z
U601 | 1 | ZXGD3009E6 | ZXGD3009E6TADICT-ND | Package_TO_SOT_SMD:SOT-23-6
Y201 | 1 | 25M | 644-1041-1-ND | Crystal:Crystal_SMD_5032-2Pin_5.0x3.2mm

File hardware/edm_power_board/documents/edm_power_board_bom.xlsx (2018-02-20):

Ref | Qnty | Value | Digikey | Footprint
C201, C205 | 2 | 220p | 311-1115-1-ND | Resistor_SMD:R_0805_2012Metric
C203, C301 | 2 | 22u | PCE4240CT-ND | Capacitor_SMD:CP_Elec_5x5.3
C204, C209, C202, C308, C303, C307, C402, C603, C605, C608, C610, C612, C602, C611, C613, C615 | 16 | 100n | 445-1418-1-ND | Capacitor_SMD:C_0805_2012Metric
C206, C306 | 2 | 10n | 490-1664-1-ND | Capacitor_SMD:C_0805_2012Metric
C207, C607, C614 | 3 | 470n | 1276-1074-1-ND | Capacitor_SMD:C_0805_2012Metric
C208, C312 | 2 | 1n | 399-1147-1-ND | Capacitor_SMD:C_0805_2012Metric
C210 | 1 | 3n3 | 311-1131-1-ND | Capacitor_SMD:C_0805_2012Metric
C211, C606, C609 | 3 | 10u | PCE4209CT-ND | Capacitor_SMD:CP_Elec_6.3x5.3
C309, C305, C304, C302, C403, C604 | 6 | 1u | 587-2910-1-ND | Capacitor_SMD:C_0805_2012Metric
C310 | 1 | 120n | 1276-6518-1-ND | Capacitor_SMD:C_0805_2012Metric
C311 | 1 | 560p | 399-3492-1-ND | Capacitor_SMD:C_0805_2012Metric
C313, C314, C315, C316 | 4 | 470n | 445-13461-1-ND | Capacitor_SMD:C_1812_4532Metric
C401, C601 | 2 | 330n | 1276-6813-1-ND | Capacitor_SMD:C_0805_2012Metric
C501 | 1 | 1800p | 490-3479-1-ND | Capacitor_SMD:C_2220_5650Metric
D201 | 1 | TL431AIDBZR | 296-17329-1-ND | Package_TO_SOT_SMD:SOT-23
D202, D302 | 2 | S2JTR | 1655-1739-1-ND | Diode_SMD:D_SMB
D301, D604, D606 | 3 | 4V7 | BZT52C4V7-13FDICT-ND | Diode_SMD:D_SOD-123
D601, D603, D607 | 3 | RS1MTR | 1655-1501-1-ND | Diode_SMD:D_SMA
D602, D605 | 2 | VS-15EWL06FNTR-M3 | VS-15EWL06FNTR-M3CT-ND | Package_TO_SOT_SMD:TO-252-2
D608 | 1 | 1.5SMC400CA | 1.5SMC400CACT-ND | Diode_SMD:D_SMC
J501 | 1 | Conn_02x08_Odd_Even | ED10523-ND | Connector_PinHeader_2.54mm:PinHeader_2x08_P2.54mm_Vertical
J502, JJ503, JJ504 | 3 | Conn_01x02 | ED1609-ND | TerminalBlock:TerminalBlock_bornier-2_P5.08mm
L201 | 1 | 6u8 | 732-4233-1-ND | Inductor_SMD:L_Wuerth_HCI-2212
L301 | 1 | 1m | 553-3686-1-ND | Inductor_SMD:L_Pulse_PA4320
Q201 | 1 | SUD19P06-60 | SUD19P06-60-GE3CT-ND | Package_TO_SOT_SMD:TO-252-2
Q301, Q303, Q304 | 3 | BSS214NW | BSS214NWH6327XTSA1CT-ND | Package_TO_SOT_SMD:SOT-323_SC-70
Q302 | 1 | BSC13DN30NSFD | BSC13DN30NSFDATMA1CT-ND | Package_TO_SOT_SMD:TDSON-8-1
Q601 | 1 | IPD50R3K0CE | IPD50R3K0CEAUMA1CT-ND | Package_TO_SOT_SMD:TO-252-2
Q602 | 1 | IPD50R380CE | IPD50R380CEAUMA1CT-ND | Package_TO_SOT_SMD:TO-252-2
R201, R207, R202, R203, R301, R306, R610, R616, R617 | 9 | 27k | 311-27.0KCRCT-ND | Resistor_SMD:R_0805_2012Metric
R204, R208, R603, R608 | 4 | 4k7 | 311-4.70KCRCT-ND | Resistor_SMD:R_0805_2012Metric
R205 | 1 | 243k | YAG1838CT-ND | Resistor_SMD:R_0805_2012Metric
R206 | 1 | 10R | 311-10.0CRCT-ND | Resistor_SMD:R_0805_2012Metric
R209 | 1 | 100R | 311-100CRCT-ND | Resistor_SMD:R_0805_2012Metric
R210 | 1 | 6k34 | 311-6.34KCRCT-ND | Resistor_SMD:R_0805_2012Metric
R211 | 1 | 10m | CRA2512-FZ-R010ELFCT-ND | Resistor_SMD:R_2512_6332Metric
R212 | 1 | 47k | 311-47.0KCRCT-ND | Resistor_SMD:R_0805_2012Metric
R213 | 1 | 15k | 311-15.0KCRCT-ND | Resistor_SMD:R_0805_2012Metric
R214, R217, R220, R218, R221, R215, R216 | 7 | 1k | 311-1.00KCRCT-ND | Resistor_SMD:R_0805_2012Metric
R219 | 1 | 20m | CSSH2728FT20L0CT-ND | Resistor_SMD:R_Stackpole_CSSH2728_4-100m
R302 | 1 | 2k2 | 311-2.20KCRCT-ND | Resistor_SMD:R_0805_2012Metric
R304, R606, R612, R615, R618, R621, R622 | 7 | 21k | 311-21.0KCRCT-ND | Resistor_SMD:R_0805_2012Metric
R305 | 1 | 3k | 311-3.00KCRCT-ND | Resistor_SMD:R_0805_2012Metric
R307, R303, R611 | 3 | 84k5 | 311-84.5KCRCT-ND | Resistor_SMD:R_0805_2012Metric
R308, R316 | 2 | 26k1 | 311-26.1KCRCT-ND | Resistor_SMD:R_0805_2012Metric
R309 | 1 | 10k5 | 311-10.5KCRCT-ND | Resistor_SMD:R_0805_2012Metric
R311, R310 | 2 | 93k1 | 311-93.1KCRCT-ND | Resistor_SMD:R_1206_3216Metric
R312 | 1 | 10k | 311-10.0KCRCT-ND | Resistor_SMD:R_0805_2012Metric
R313 | 1 | 52k3 | 311-52.3KCRCT-ND | Resistor_SMD:R_0805_2012Metric
R314 | 1 | 102R | 311-102CRCT-ND | Resistor_SMD:R_0805_2012Metric
R315 | 1 | 150m | 311-0.15TCT-ND | Resistor_SMD:R_2512_6332Metric
R317 | 1 | 2M1 | 311-2.10MCRCT-ND | Resistor_SMD:R_0805_2012Metric
R318 | 1 | 18k | 311-18.0KCRCT-ND | Resistor_SMD:R_0805_2012Metric
R501 | 1 | 1M | 311-1.00MFRCT-ND | Resistor_SMD:R_1206_3216Metric
R601, R604, R605, R609 | 4 | 4R99 | 311-4.99CRCT-ND | Resistor_SMD:R_0805_2012Metric
R602, R607 | 2 | 47R | 311-47.0CRCT-ND | Resistor_SMD:R_0805_2012Metric
R613, R614, R619, R620, R623, R624 | 6 | 187k | 311-187KCRCT-ND | Resistor_SMD:R_0805_2012Metric
RV201 | 1 | 50k | 3314G-503ECT-ND | Potentiometer_SMD:Potentiometer_Bourns_3314G_Horizontal
RV601 | 1 | 100k | 3314G-104ECT-ND | Potentiometer_SMD:Potentiometer_Bourns_3314G_Horizontal
RV602 | 1 | 500k | 3314G-504ECT-ND | Potentiometer_SMD:Potentiometer_Bourns_3314G_Horizontal
U201 | 1 | LM358 | LM358F-GE2CT-ND | Package_SO:SOIC-8_3.9x4.9mm_P1.27mm
U202 | 1 | LM25085MM | LM25085MM/NOPBCT-ND | Package_SO:MSOP-8_3x3mm_P0.65mm
U301 | 1 | Si8641BB-B-IS | SI8641BB-B-IS-ND | Package_SO:SOIC-16W_7.5x10.3mm_P1.27mm
U302 | 1 | LM5022MM | LM5022MM/NOPBCT-ND | Package_SO:MSOP-10_3x3mm_P0.5mm
U303, U605, U606 | 3 | LM311 | LM311MX/NOPBCT-ND | Package_SO:SOIC-8_3.9x4.9mm_P1.27mm
U401 | 1 | L78L05_SO8 | 497-1182-1-ND | Package_SO:SOIC-8_3.9x4.9mm_P1.27mm
U601 | 1 | Si8642BB-B-IS | SI8642BB-B-IS-ND | Package_SO:SOIC-16W_7.5x10.3mm_P1.27mm
U602 | 1 | L7815 | 497-1179-1-ND | Package_TO_SOT_SMD:TO-263-2
U603, U604 | 2 | FAN7171 | FAN7171MX-F085FSCT-ND | Package_SO:SOIC-8_3.9x4.9mm_P1.27mm

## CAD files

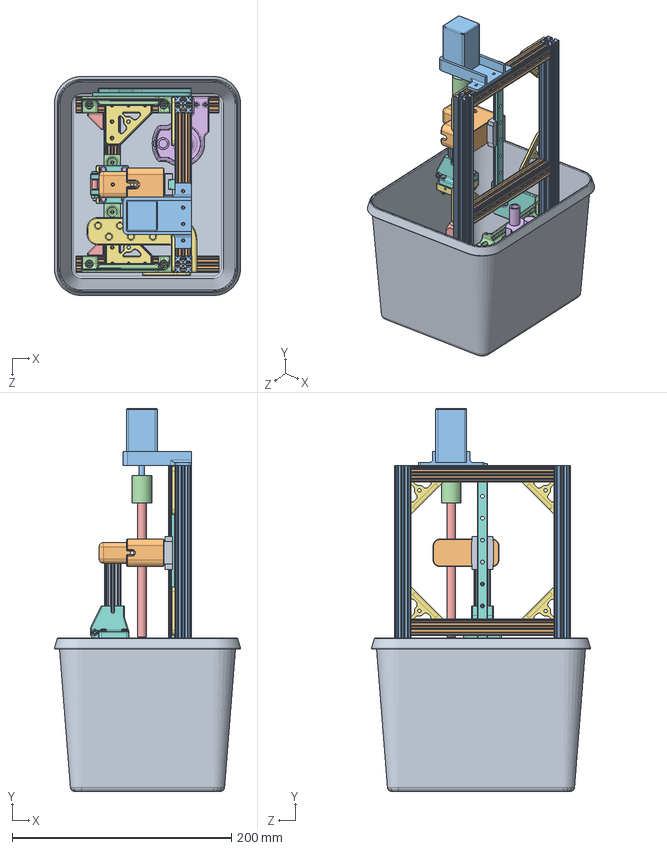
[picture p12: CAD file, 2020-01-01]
hardware/edm_machine/cad/edm_machine.SLDASM
169.7 x 349.0 x 199.7 mm
openbeam_130mm x 5
openbeam_280mm x 2
stamp_holder
stamp_blank_15mm
water_pump
openbeam_l_plate x 8
linear_rail_lwl9_bcs_160mm
linear_bearing_lwl9_bcs
slide_holder
stepper28bygh
stepper_flexible_coupler_5mm_8mm
trapezoidal_8mm_130mm
trapezoidal_nut_8mm
template_holder_bottom
template_holder_top
template_holder_spring
template
screw_m3_25
nut_m3 x 5
template_holder_electrode
screw_m3_20 x 4
screw_m3_12
screw_m3_6 x 4
openbeam_70mm
slide_bar_holder
stepper_holder
bracket_big_l x 2
bracket_small_angle x 2
water_pump_holder
magnet_holder
water_hose_holder

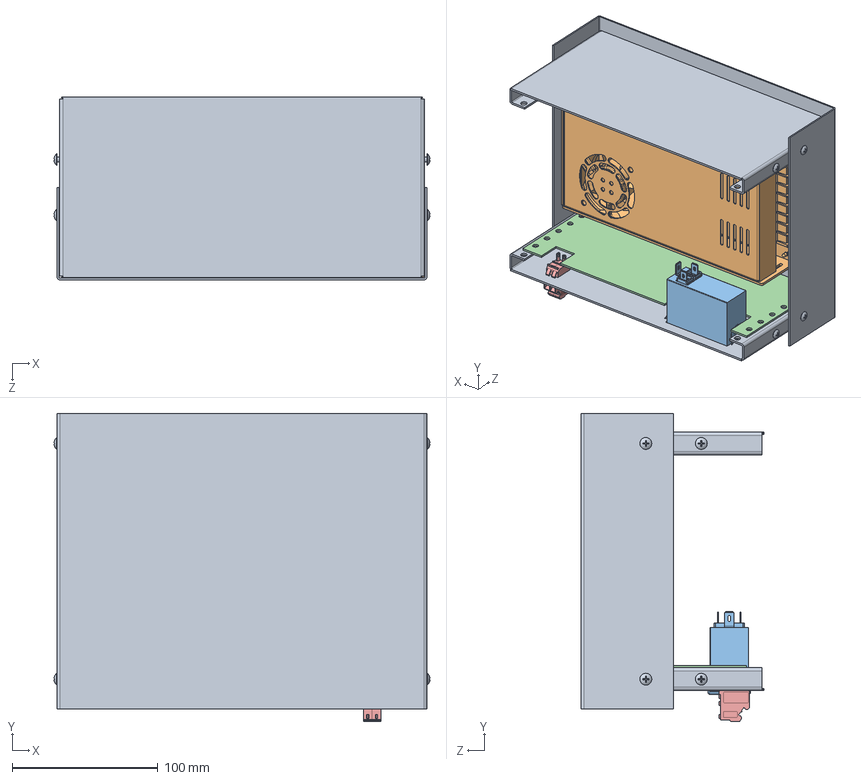
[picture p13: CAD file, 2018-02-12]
hardware/mechanics/cad/edm_power_box.SLDASM
258.3 x 211.7 x 125.5 mm
1458G5
s-360
06AK2D
power_pcb
panelkontakt_0706016_02 x 2

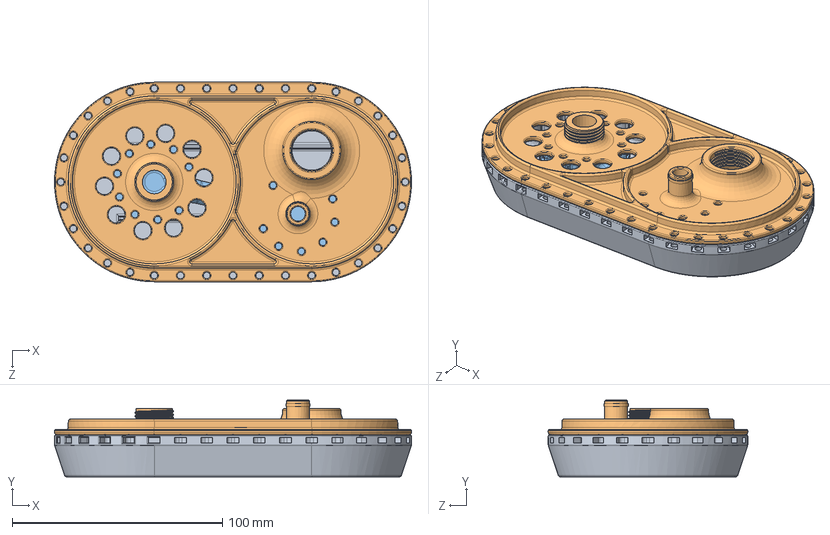
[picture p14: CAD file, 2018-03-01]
hardware/edm_machine/cad/oil_filter_holder.SLDASM
170.0 x 36.5 x 95.0 mm
oil_filter_holder_bottom
oil_filter_holder
oil_filter_holder_inlet x 2

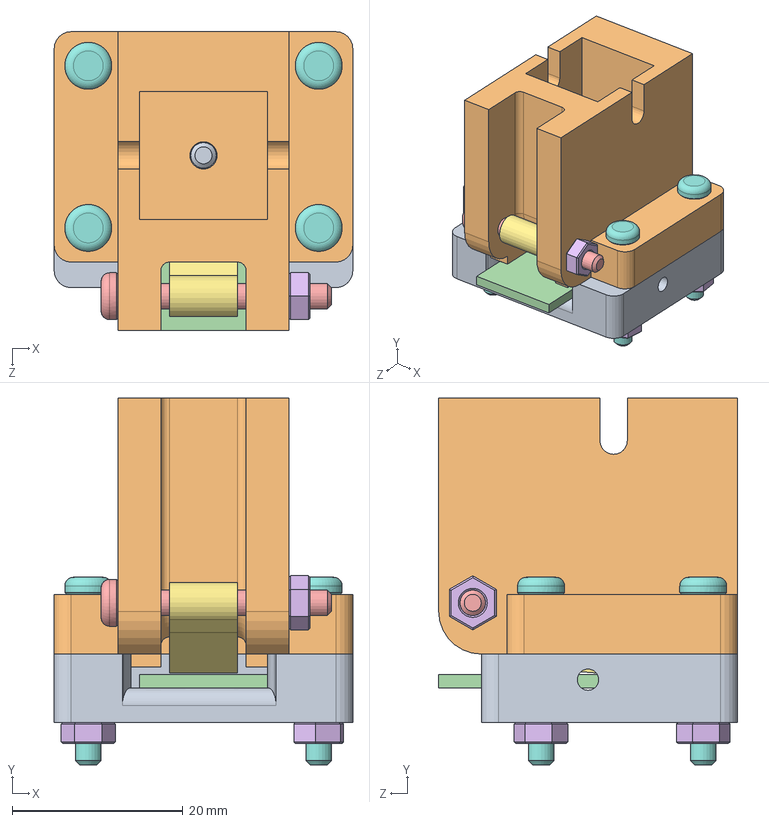
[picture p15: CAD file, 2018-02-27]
hardware/edm_machine/cad/template_holder.SLDASM
35.0 x 43.0 x 35.0 mm
template_holder_bottom
template_holder_top
template_holder_spring
template
screw_m3_25
nut_m3 x 5
template_holder_electrode
screw_m3_20 x 4
screw_m3_12

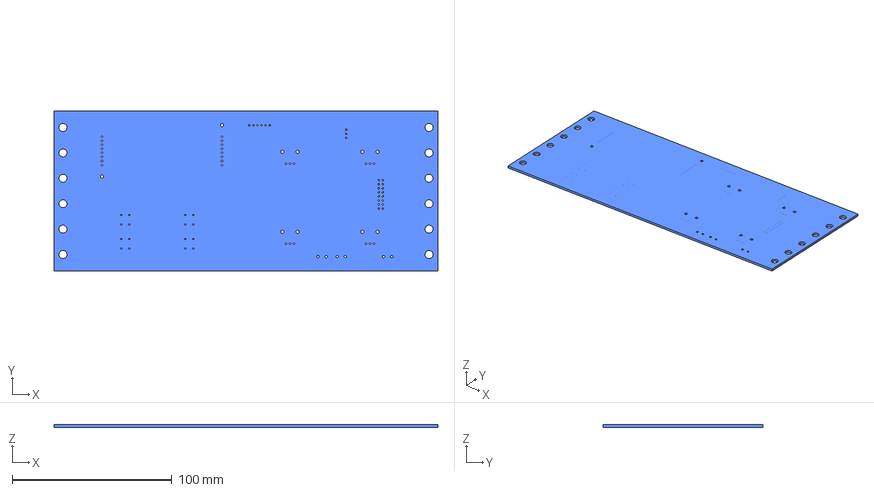
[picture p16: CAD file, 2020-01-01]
hardware/edm_control_board/cad/edm_control_board1.step
240.0 x 100.0 x 1.60 mm
Pcb
Step_Models

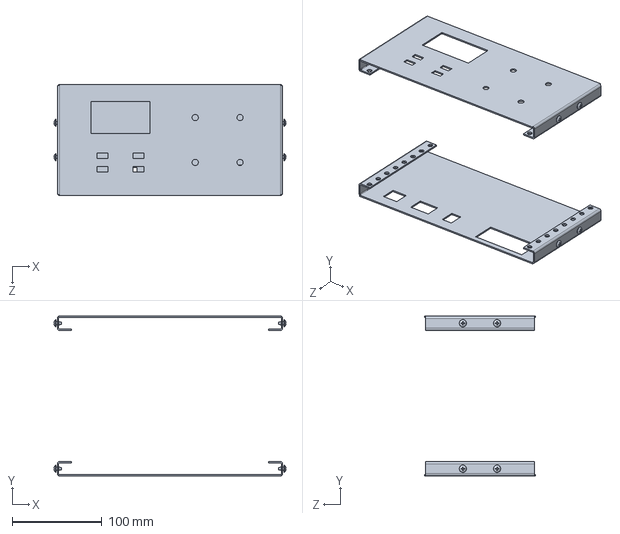
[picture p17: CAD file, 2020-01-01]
hardware/edm_control_box/cad/1458G5.SLDPRT
258.3 x 177.8 x 124.0 mm

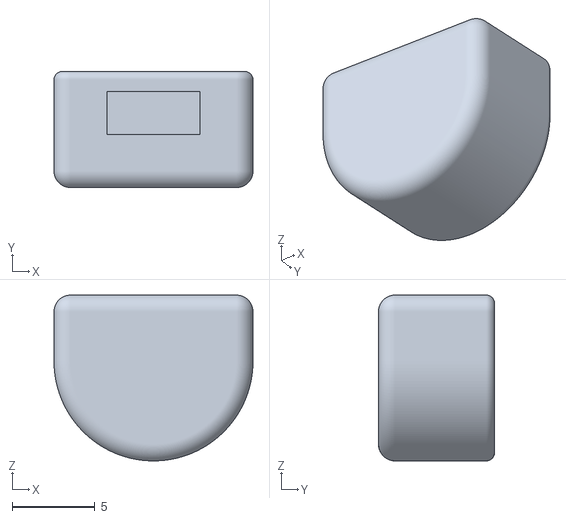
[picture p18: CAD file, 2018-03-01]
hardware/edm_machine/cad/stl/m3holder.STL
12.0 x 7.00 x 10.0

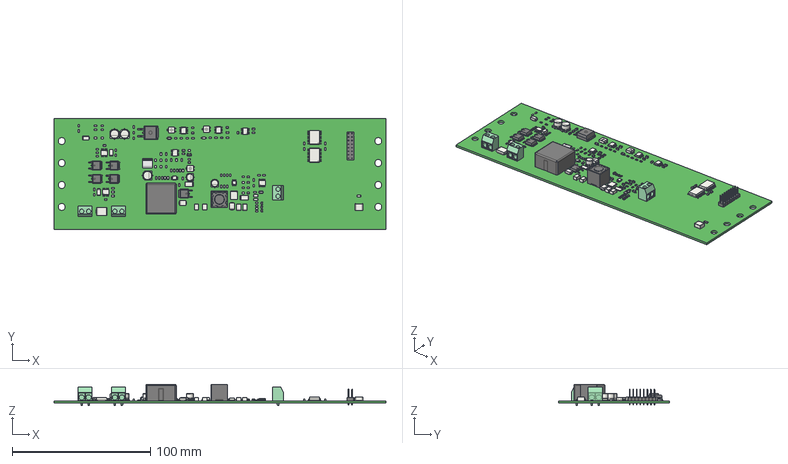
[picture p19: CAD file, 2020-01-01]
hardware/edm_power_board/cad/edm_power_board.FCStd
240.0 x 80.0 x 15.5 mm
Pcb
R_0805_2012Metric_
R_0805_2012Metric_001
C_1812_4532Metric_
C_1812_4532Metric_001
C_0805_2012Metric_
D_SMC_
TerminalBlock_bornier-2_P5.08mm_
D_SMA_
R_0805_2012Metric_002
R_0805_2012Metric_003
PinHeader_2x08_P254mm_Vertical_
L_Pulse_PA4320_
R_0805_2012Metric_004
C_0805_2012Metric_001
CP_Elec_5x5.3_
C_0805_2012Metric_002
R_0805_2012Metric_005
C_0805_2012Metric_003
C_0805_2012Metric_004
C_0805_2012Metric_005
C_0805_2012Metric_006
C_0805_2012Metric_007
CP_Elec_6.3x5.3_
C_0805_2012Metric_008
C_0805_2012Metric_009
C_0805_2012Metric_010
C_0805_2012Metric_011
C_0805_2012Metric_012
C_0805_2012Metric_013
C_0805_2012Metric_014
C_0805_2012Metric_015
C_0805_2012Metric_016
C_0805_2012Metric_017
C_0805_2012Metric_018
C_1812_4532Metric_002
C_1812_4532Metric_003
C_0805_2012Metric_019
C_0805_2012Metric_020
C_0805_2012Metric_021
C_0805_2012Metric_022
C_0805_2012Metric_023
C_0805_2012Metric_024
C_0805_2012Metric_025
C_0805_2012Metric_026
CP_Elec_6.3x5.3_001
C_0805_2012Metric_027
C_0805_2012Metric_028
CP_Elec_6.3x5.3_002
C_0805_2012Metric_029
C_0805_2012Metric_030
C_0805_2012Metric_031
C_0805_2012Metric_032
C_0805_2012Metric_033
SOT_23_
D_SMB_
D_SOD_123_
D_SMB_001
D_SMA_001
TO_252_2_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

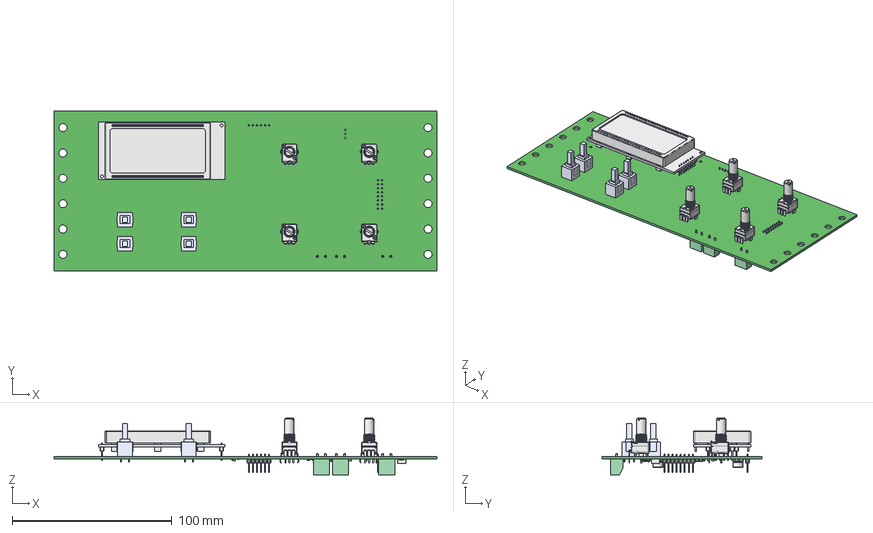
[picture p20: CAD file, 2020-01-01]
hardware/edm_control_board/cad/edm_control_board.FCStd
240.0 x 100.0 x 35.6 mm
Pcb
PVA1_
PVA1_001
PVA1_002
PVA1_003
Potentiometer_TT_P0915N_
Potentiometer_TT_P0915N_001
Potentiometer_TT_P0915N_002
Potentiometer_TT_P0915N_003
NHD-0420H1Z_
C_2220_5650Metric_
PinHeader_2x08_P254mm_Vertical_
PinHeader_1x06_P254mm_Vertical_
R_1206_3216Metric_
C_0805_2012Metric_
C_0805_2012Metric_001
C_0805_2012Metric_002
C_0805_2012Metric_003
C_0805_2012Metric_004
C_0805_2012Metric_005
R_0805_2012Metric_
R_0805_2012Metric_001
CP_Elec_6.3x5.3_
CP_Elec_6.3x5.3_001
C_0805_2012Metric_006
C_0805_2012Metric_007
C_0805_2012Metric_008
C_0805_2012Metric_009
C_0805_2012Metric_010
C_0805_2012Metric_011
C_0805_2012Metric_012
C_0805_2012Metric_013
C_0805_2012Metric_014
C_0805_2012Metric_015
SOIC_8_39x49mm_P127mm_
SOT_323_SC_70_
SOT_323_SC_70_001
SOT_323_SC_70_002
SOT_323_SC_70_003
R_0805_2012Metric_002
R_0805_2012Metric_003
R_0805_2012Metric_004
R_0805_2012Metric_005
R_0805_2012Metric_006
LQFP_64_10x10mm_P05mm_
TerminalBlock_bornier-2_P5.08mm_
TerminalBlock_bornier-2_P5.08mm_001
TerminalBlock_bornier-2_P5.08mm_002

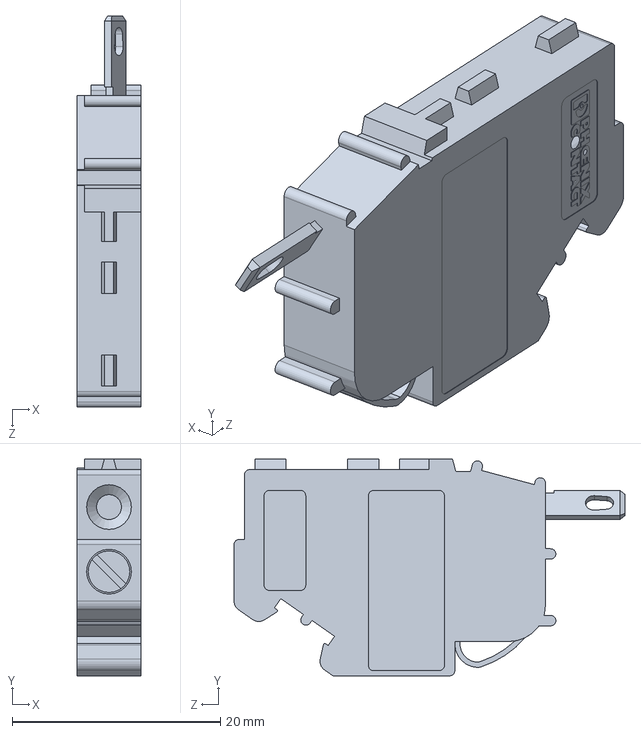
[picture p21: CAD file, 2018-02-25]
hardware/edm_control_box/cad/panelkontakt_0706016_02.SLDPRT
6.10 x 20.8 x 37.5 mm

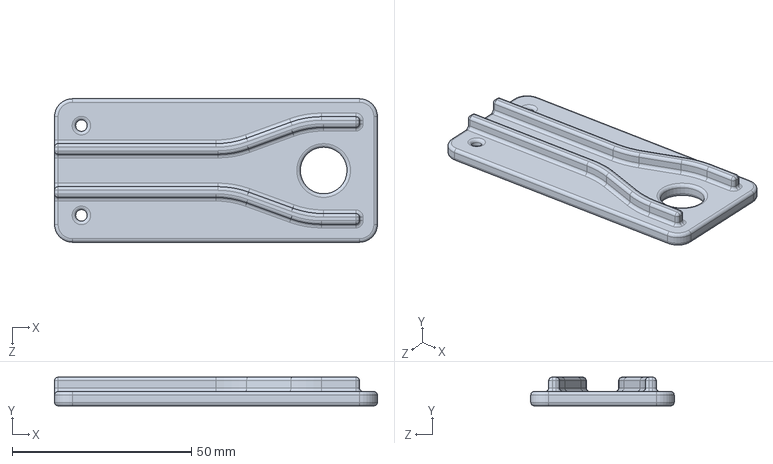
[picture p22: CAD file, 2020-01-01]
hardware/edm_machine/cad/water_hose_holder.SLDPRT
90.0 x 8.00 x 40.0 mm

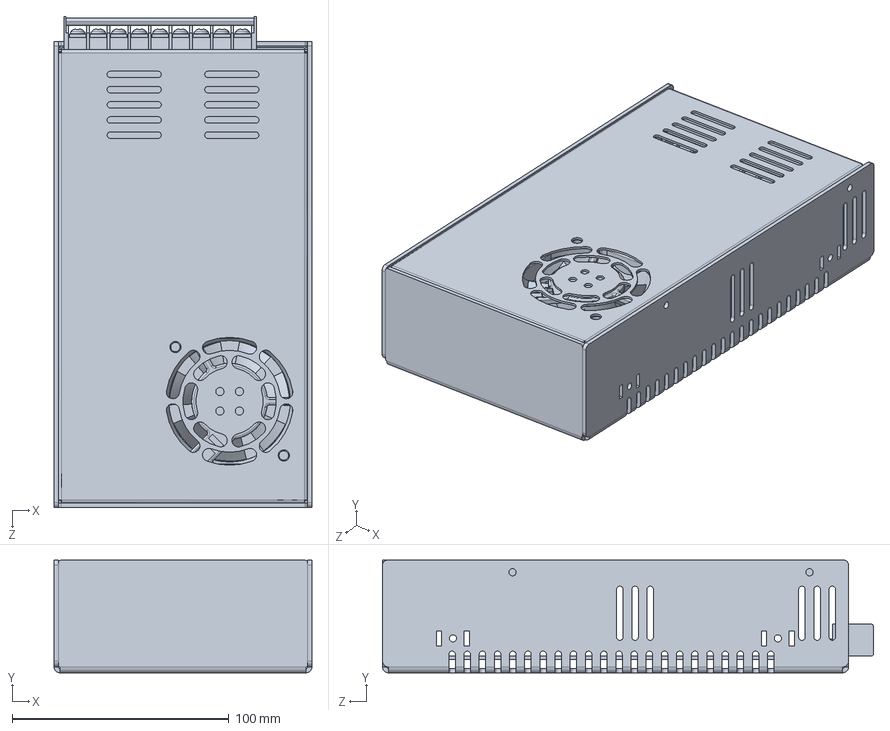
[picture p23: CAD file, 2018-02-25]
hardware/edm_control_box/cad/s-360.SLDPRT
119.0 x 52.0 x 226.5 mm

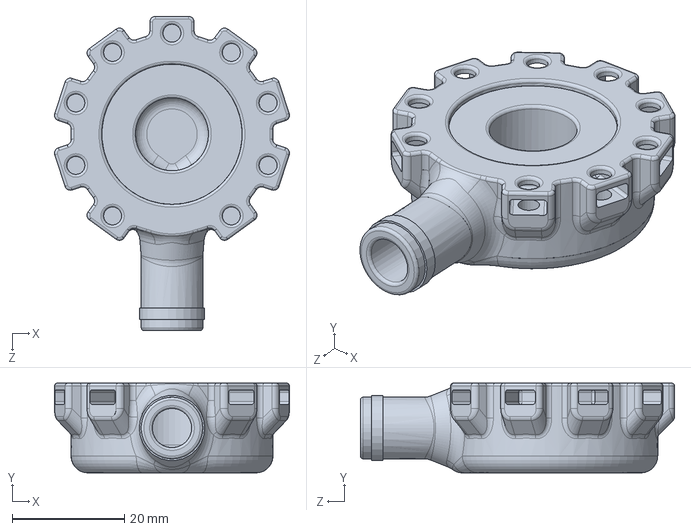
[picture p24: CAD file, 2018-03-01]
hardware/edm_machine/cad/oil_filter_holder_inlet.SLDPRT
41.9 x 16.0 x 56.0 mm

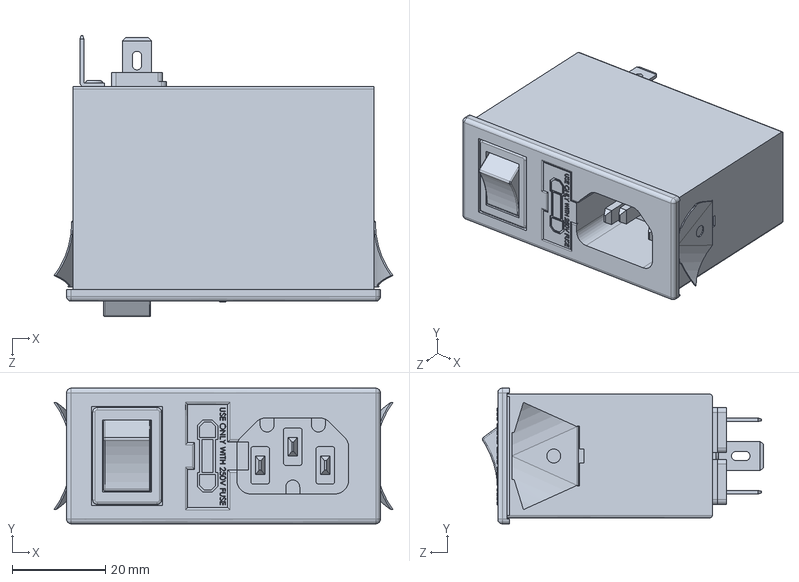
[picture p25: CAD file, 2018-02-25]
hardware/edm_control_box/cad/06AK2D.SLDPRT
72.7 x 29.1 x 60.3 mm

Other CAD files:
hardware/edm_machine/cad/test/m3holder.SLDPRT
hardware/edm_machine/cad/oil_filter_holder_bottom.SLDPRT
hardware/edm_control_box/cad/DQ420MA.SLDPRT
hardware/edm_machine/cad/openbeam_75mm.SLDPRT
hardware/edm_control_box/cad/COM-10002.SLDPRT
hardware/edm_control_box/cad/button_PE.SLDPRT
hardware/edm_machine/cad/bracket_big_l.SLDPRT
hardware/edm_machine/cad/bracket_small_angle.SLDPRT
hardware/edm_machine/cad/linear_bearing_lwl9_bcs.SLDPRT
hardware/edm_machine/cad/linear_rail_lwl9_bcs_160mm.SLDPRT
hardware/edm_machine/cad/magnet_holder.SLDPRT
hardware/edm_machine/cad/nut_m3.SLDPRT
hardware/edm_machine/cad/oil_filter_holder.SLDPRT
hardware/edm_machine/cad/oil_filter_holder_inlet_2.SLDPRT
hardware/edm_machine/cad/openbeam_120mm.SLDPRT
hardware/edm_machine/cad/openbeam_130mm.SLDPRT
hardware/edm_machine/cad/openbeam_180mm.SLDPRT
hardware/edm_machine/cad/openbeam_280mm.SLDPRT
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

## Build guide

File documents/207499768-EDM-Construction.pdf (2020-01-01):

### Dick Penny’s EDM

### 1. Introduction

The motivation to embark upon this project came when I broke (not for the first time) a tap in something I was making. I could have put the hole somewhere else which would have been ugly, or re-made the piece which would have been tedious as it involved re-making the mating part as well, so I investigated alternatives. As this happened close to Christmas I put Ben Fleming’s ‘EDM How To’ book on my wish-list for holiday reading and became hooked on the idea of making an EDM machine.

I thought these words and pictures might be of assistance to those embarking on the same exercise. There are some pictures at the end and a short video clip to prove it worked !

The original design idea was to use the chassis and cover from a redundant PC to house the spark generator and control electronics. However a friend was clearing out his garage and came across an old 12/24v DC – 240v AC inverter which was housed in a rather interesting box, so I used that instead.

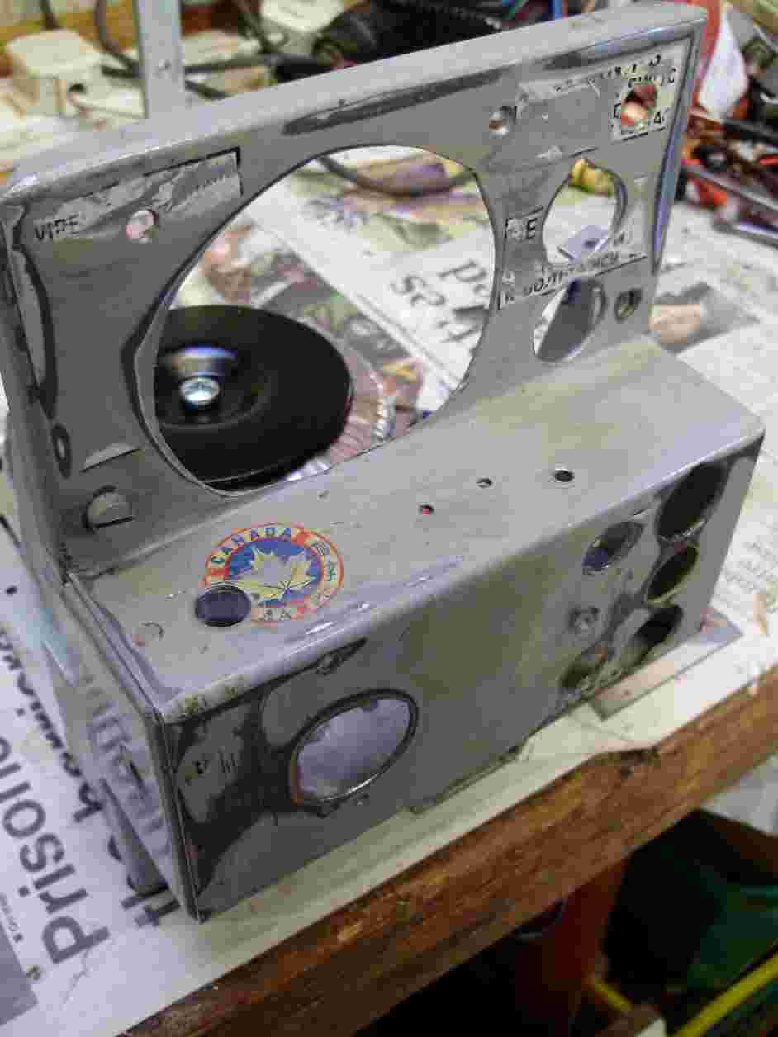
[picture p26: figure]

The chassis in the process of being re-worked is shown above. It probably dates from the 1960’s by the look of the components that were contained in it, and was reputed to be of US military origin (there is a Canadian emblem that appeared when the paint was sanded off). The material cut and behaved like Aluminium, but strangely it was slightly magnetic, and I persuaded a colleague to analyse the metal. It is 30% Cadmium (I didn’t sand and grind much more, and it is now coated in paint again !)

I would be interested in any ideas as to where it came from.

### 2. Electronics

For people building an EDM in the UK, the following parts list may be useful

Farnell Order
Code | # Rqd | Description
3851825 | 2 | C1, 2 20uf 250v AC Polycarbonate capacitor
9696300 | 1 | C3 150uf 200v DC capacitor
1198665 | 1 | C4 1000uf 160v DC capacitor
8126593 | 1 | C5 1000uf 35v capacitor
1457590 | 5 * | C6 6.8uf 35v capacitor
1216440 | 5 * | C7, 8, 9, C9a (motor upgrade) 100nf 50v capacitor
1281820 | 1 | C10 22uf capacitor (pcb upgrade)
4084810 | 1 | D1 6A 100v bridge rectifier
1017647 | 1 | D2 2A 400V bridge rectifier
9556125 | 2 | D4, 5 3A 100v diode
1619326 | 1 | R1+2 150W 10R resistor
1265082 | 5 * | R3, 6, 7, 8, 14 33k resistor
1265072 | 5 * | R4, 9, 11a, 15, 16, 1k resistor
8557470 | 1 | R5 50k potentiometer
1265085 | 5 * | R10 100k resistor
1265077 | 5 * | R12 4.7k resistor
1634659 | 1 | SW1 AC on/off. Red illuminated
1634647 | 2 | SW2, 3 cutting power selection switches
1634645 | 1 | SW3 servo on/off
1634666 | 4 | Splash proof switch covers
1086634 | 1 | SW5 electrode up (black)
1086635 | 1 | SW6 electrode down (red)
9532501 | 1 | T1 2x30v 300VA torroid transformer
1675045 | 1 | T3 2x12v 15VA torroid transformer
9756132 | 1 | U1 12v regulator
1470411 | 1 | U2 SN75441ONE controller
9487670 | 1 | U3 LM-339 comparitor
8576378 | 5 * | 5mm LED holders
1641934 | 8 | PCB connector block
4620896 | 1 | DIP heat sink
1211706 | 2 | Heat sink foil
1077295 | 1 | 14 pin socket
1077298 | 1 | 16 pin socket
Upload to | Note: Items marked * are minimum order quantities
http://uk.farnell.com/
to place an order | At the time of purchase, torroid transformers were
| the most cost effective and best size option.
| This may change depending on primary supplier

Maplin Order Code

| These items should also be available from Farnell, but
| were purchased from Maplin for convenience
QY83E | 1 | D3 red/green 5mm LED
JM71N | 1 | R11 (mod) 10k miniature pot
UF97F | 1 | R13 100k trimmer
| 2 Heat shrink tubing selection pack

Misc items
| Panel meter 100 µA 10kΩ per volt
| 12v cooling fan salvaged from PC power supply
| Knobs for potentiometers (turned from stock material);
| Wiring (also salvaged from PC power supply)
| Fuse holder; 2 amp slow blow fuse, cable ties
| push-on crimp connectors, motor and servo connector

Redundant PC chassis and casing (see intro text)

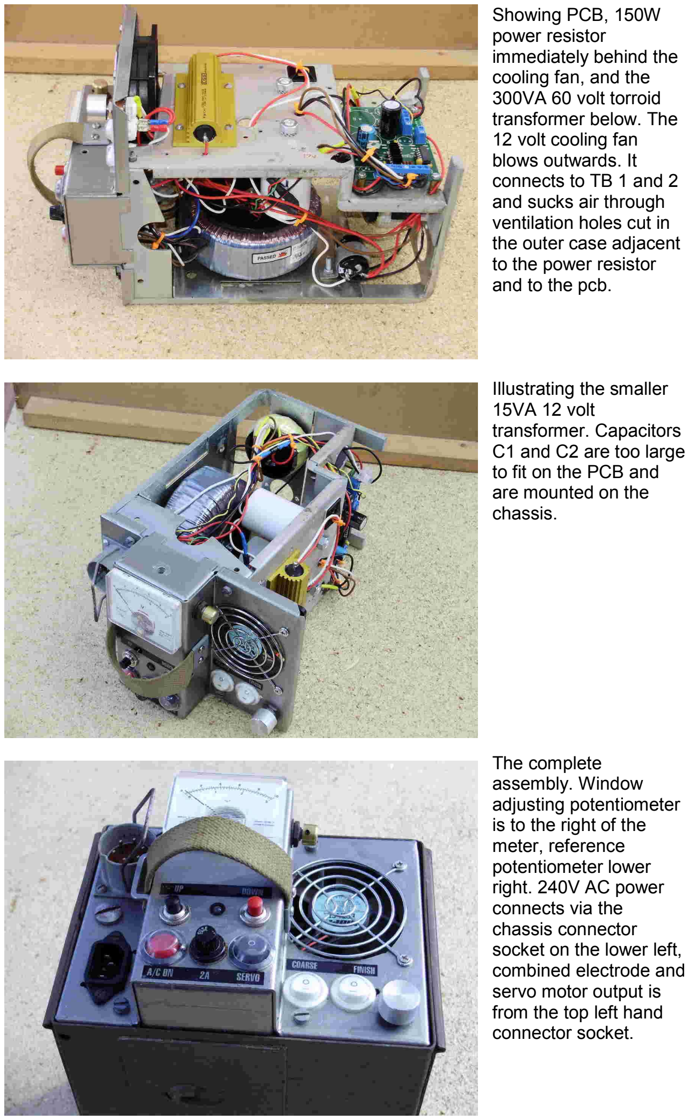
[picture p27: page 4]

Showing PCB, 150W
power resistor
immediately behind the
cooling fan, and the
300VA 60 volt torroid
transformer below. The

### 12 volt cooling fan

blows outwards. It
connects to TB 1 and 2
and sucks air through
ventilation holes cut in
the outer case adjacent
to the power resistor
and to the pcb.

Illustrating the smaller
15VA 12 volt
transformer. Capacitors
C1 and C2 are too large
to fit on the PCB and
are mounted on the
chassis.

The complete
assembly. Window
adjusting potentiometer
is to the right of the
meter, reference
potentiometer lower
right. 240V AC power
connects via the
chassis connector
socket on the lower left,
combined electrode and
servo motor output is
from the top left hand
connector socket.

### 3. Servo

Servo motor | http://www.virtualvillage.co.uk/12v-dc-60-rpm-high-torque-gear-box-motor-001480-63.html
Ball bearing drawer slide | B&Q Hardware store
Bearing | 40mm OD sealed ball race
| M8 threaded rod
| Salvaged drill chuck

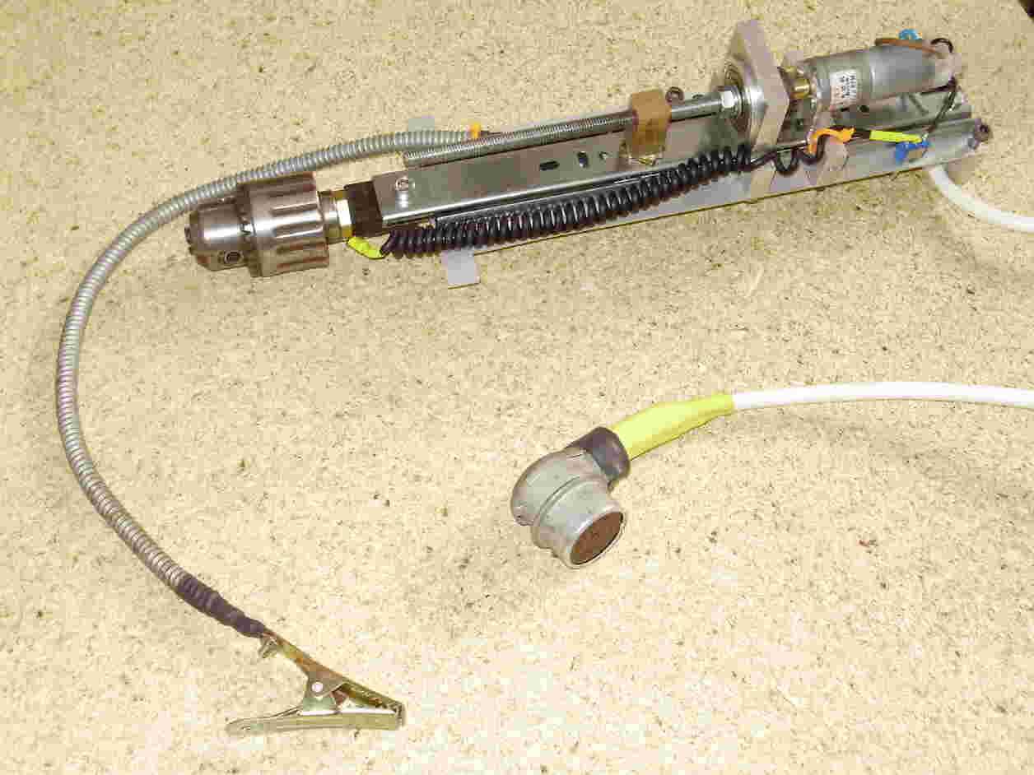
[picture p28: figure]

There is a switch at the top which isolates the electrode to allow precise positioning using the servo motor without running the risk of sparking or shocks.

The small gearbox motor from www.virtualvillage.com works well. Modest price, only draws 100 mA when running and 500 mA turning against the ball clutch.

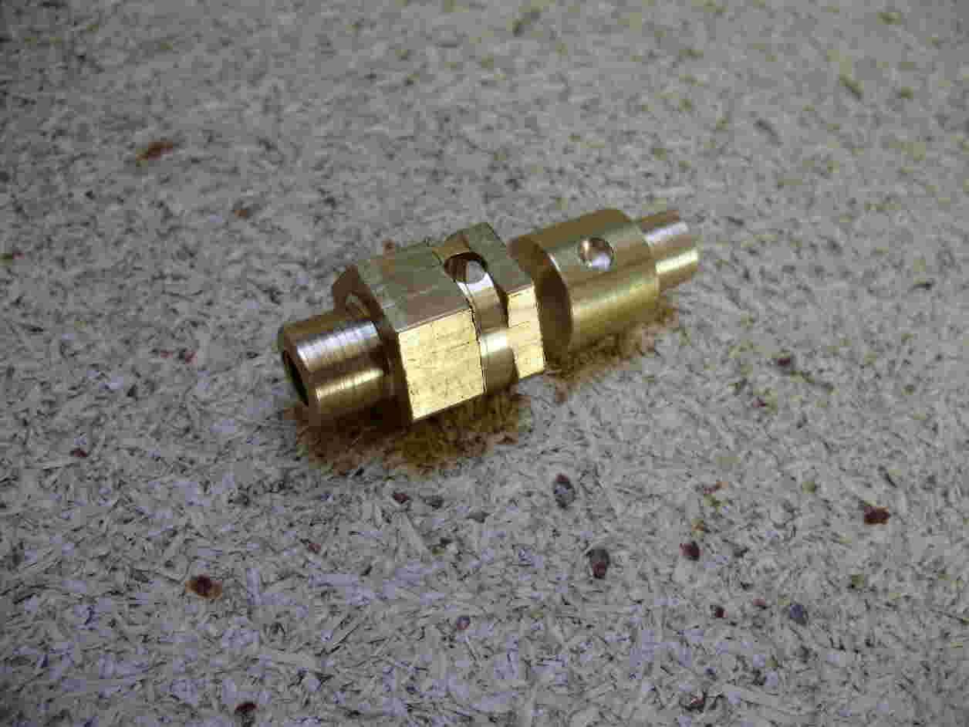
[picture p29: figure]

The ball clutch is a modification of the drawings and pictures from Rich Carlstedt shown on the EDMHomeBuilders site. Constructed from 19 mm hex brass as the outer housing and connected to the 8 mm threaded rod, held by the bearing. The housing is drilled for 3 x 5mm ball bearings and encased in heatshrink tubing which acts as the spring. Inside is a 15 mm dia. round brass rotor with dimples for the ball bearings drilled through from the outer housing, and connected to the motor shaft.

### 3. Dielectric Bath, Filter and Pump

Workpiece tank | Small plastic storage box. B&Q
Reservoir | Cooling system from lathe (Axminster Tool Centre) with
| upgraded (used) pump.
Filter | From commercial vehicle salvage yard. Uses AC72
| paper filter element
Vice | 3" machine vice (Machine Mart – Clarkes)
Hoses | 8mm braided air hose; 3/4" suction/delivery hose (Machine Mart – Clarkes); washing machine inlet hose
| Misc 15mm compression fittings and valves
Paraffin/kerosene | 10 litres

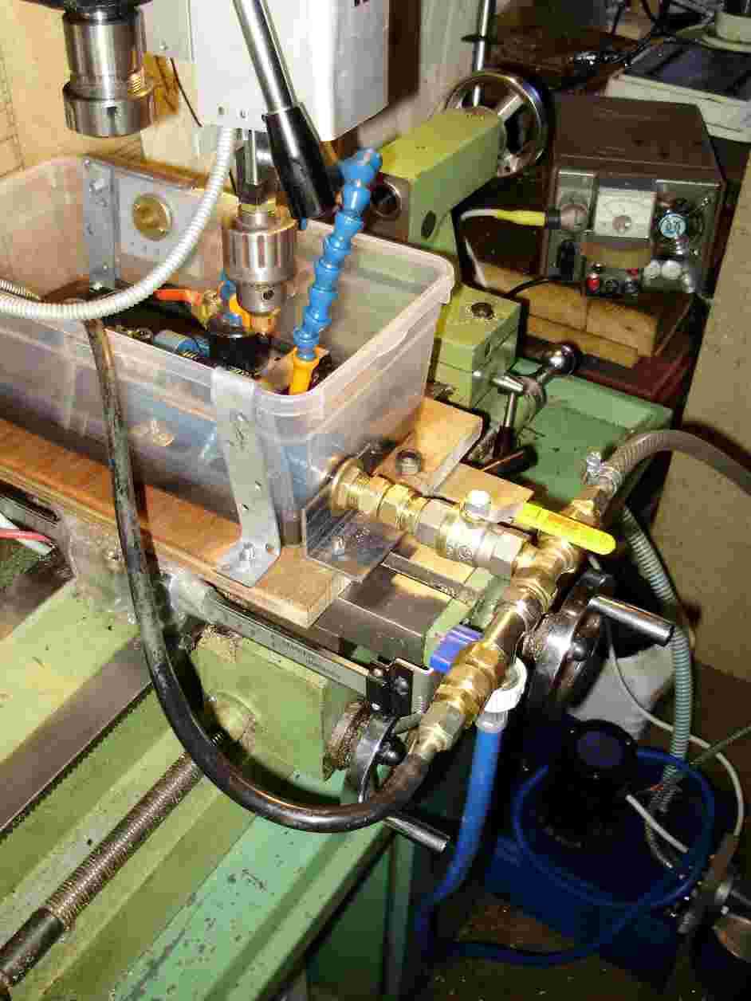
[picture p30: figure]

Space is at a premium as the servo is fixed to the milling head of a combined lathe/mill, and the work piece is positioned using the lathe cross slide.

The spark generator and control box is positioned alongside, and the dielectric reservoir and pump on the floor.

A manifold directs the flow of dielectric fluid to fill, or flush, and allows the fluid to drain back to the reservoir at the end of a burn. Filling and emptying of the dielectric bath only takes about 20 sec. A large bore overflow pipe carries fluid back to the reservoir during the burn.

The small volume in the bath means it becomes dirty very quickly, but there is a good flow of clean flushing fluid.

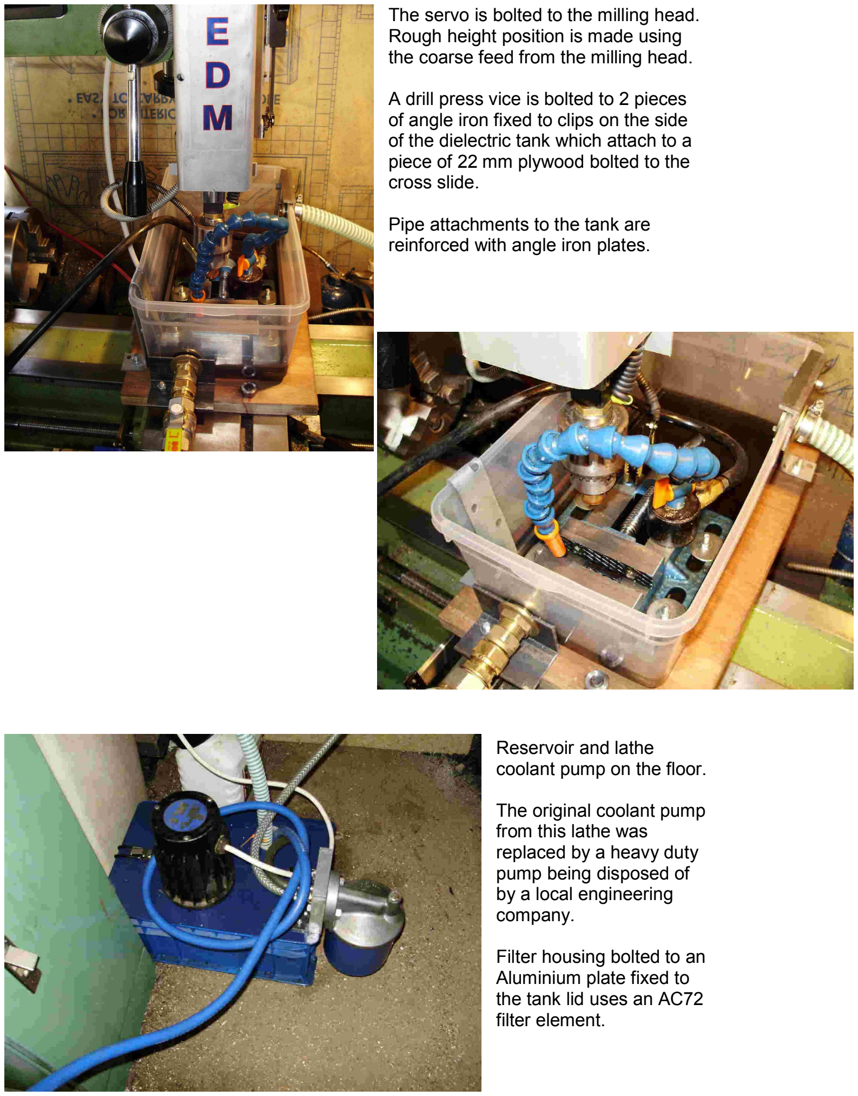
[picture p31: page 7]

The servo is bolted to the milling head. Rough height position is made using the coarse feed from the milling head.

A drill press vice is bolted to 2 pieces of angle iron fixed to clips on the side of the dielectric tank which attach to a piece of 22 mm plywood bolted to the cross slide.

Pipe attachments to the tank are reinforced with angle iron plates.

Reservoir and lathe
coolant pump on the floor.

The original coolant pump
from this lathe was
replaced by a heavy duty
pump being disposed of
by a local engineering
company.

Filter housing bolted to an Aluminium plate fixed to
the tank lid uses an AC72
filter element.

### 5. Results

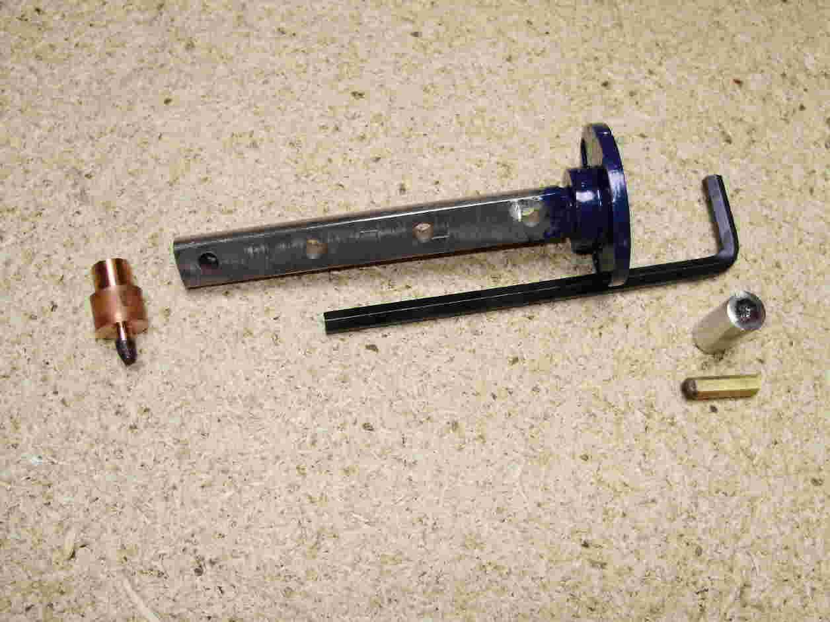
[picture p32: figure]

Stainless steel shaft with M6 tap broken in the left hand hole taken out in around 10 mins with a Copper electrode. Hole edge had been damaged from previous attempts to remove the tap, but deeper in the tap was removed leaving the tap size hole intact.

Second item is a stainless rod with a 5 mm deep 6 mm hex hole burned in using a piece of hex brass rod as the electrode. Burn was stable using full power (all capacitors switched in), but the brass eroded twice as fast as the stainless !

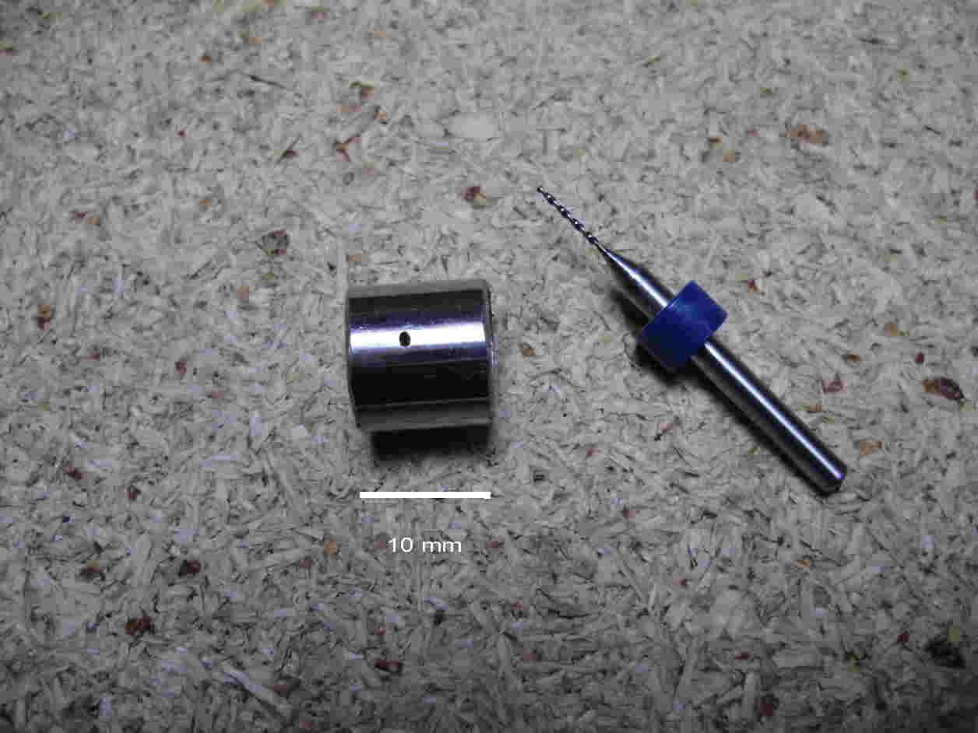
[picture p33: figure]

### 0.75 mm hole in a 10 mm dia. 1.5 mm wall thickness stainless steel tube, made in 5

mins using a solid carbide drill as the electrode on coarse cut setting. Not a very stable burn as there was a small oscillation with each spark. Four holes were made before the drill eroded away.

Video shows a burn using the brass hex electrode.

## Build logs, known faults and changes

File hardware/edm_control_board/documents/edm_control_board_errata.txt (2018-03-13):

2018-03-13
----------
Patch cable soldered between NRST on J405 and R206

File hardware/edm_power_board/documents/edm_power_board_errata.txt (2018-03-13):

2018-03-13
----------
R617 changed to 10k
R307 changed to 56k
R608 changed to 22k
R611 changed to 27k
R304, R606 and R615 changed to 470R

Patch cable soldered to +24V on U602

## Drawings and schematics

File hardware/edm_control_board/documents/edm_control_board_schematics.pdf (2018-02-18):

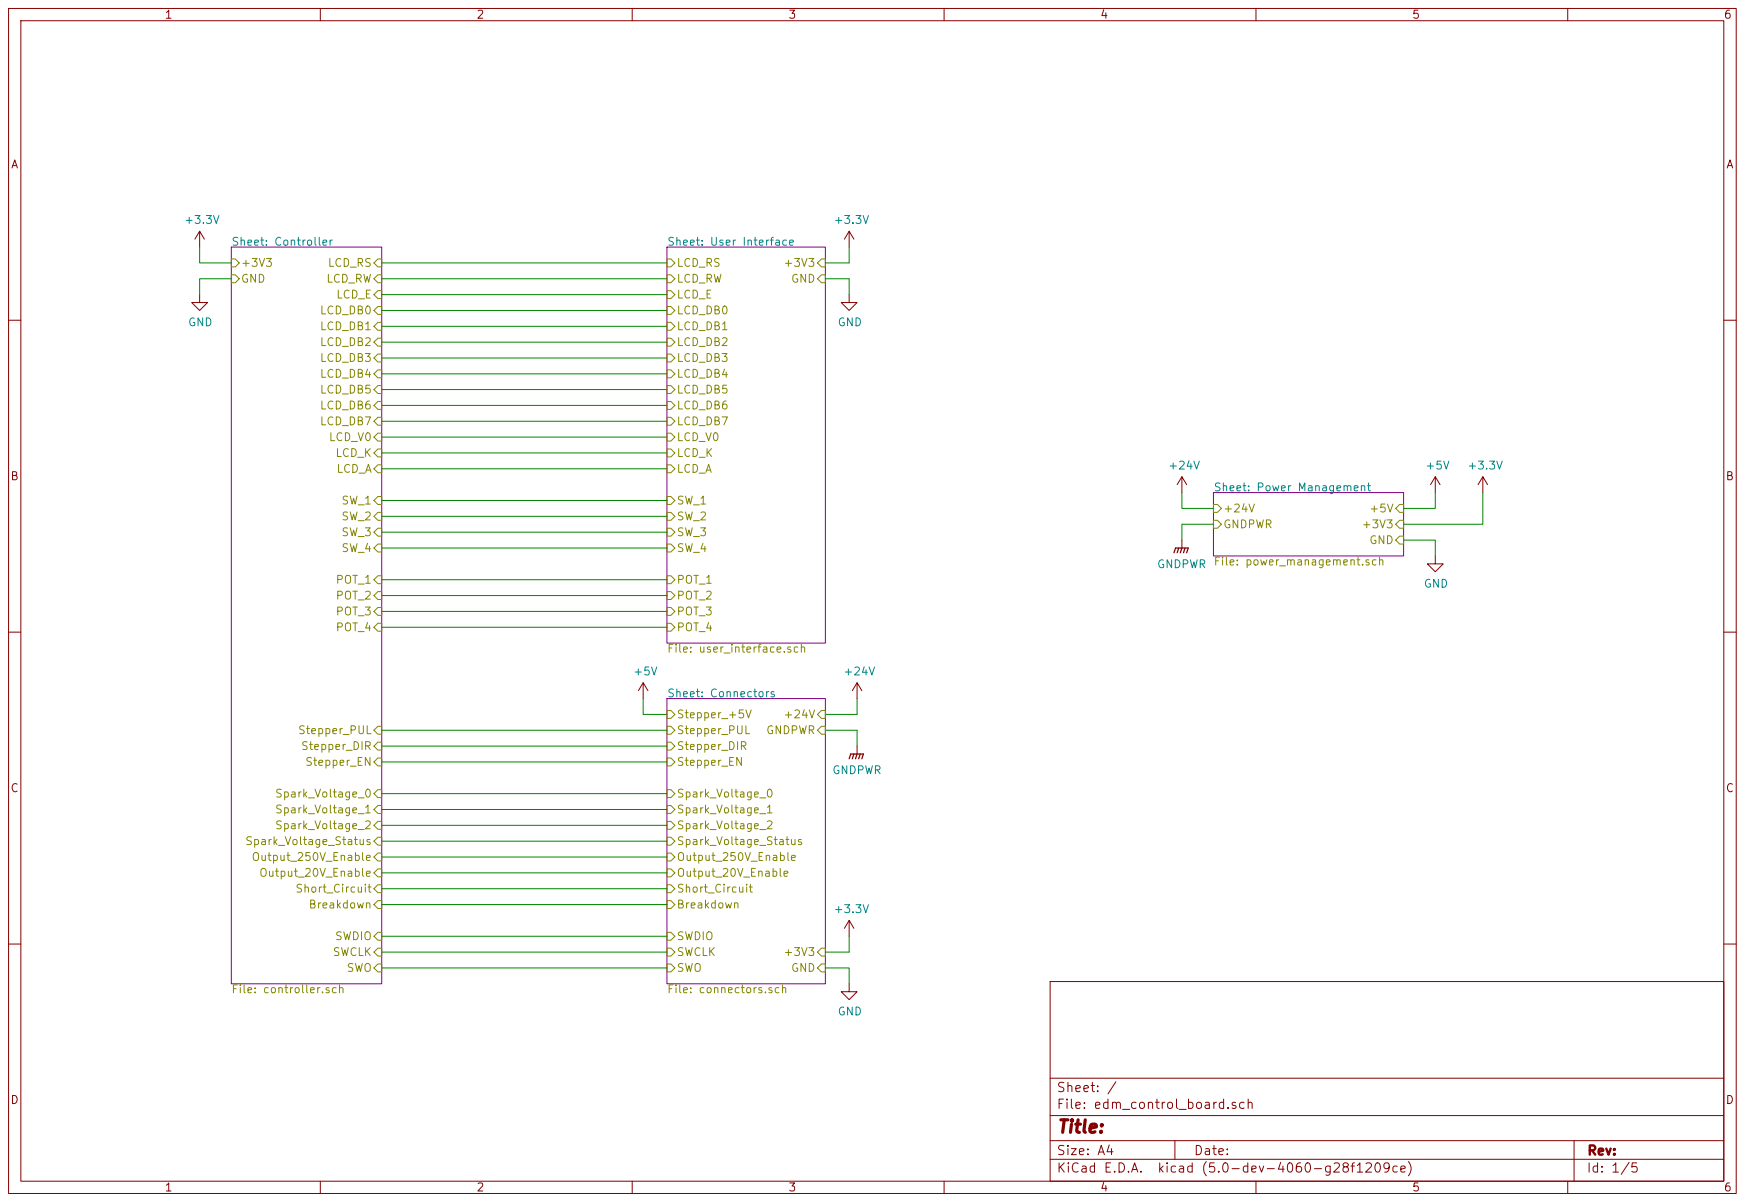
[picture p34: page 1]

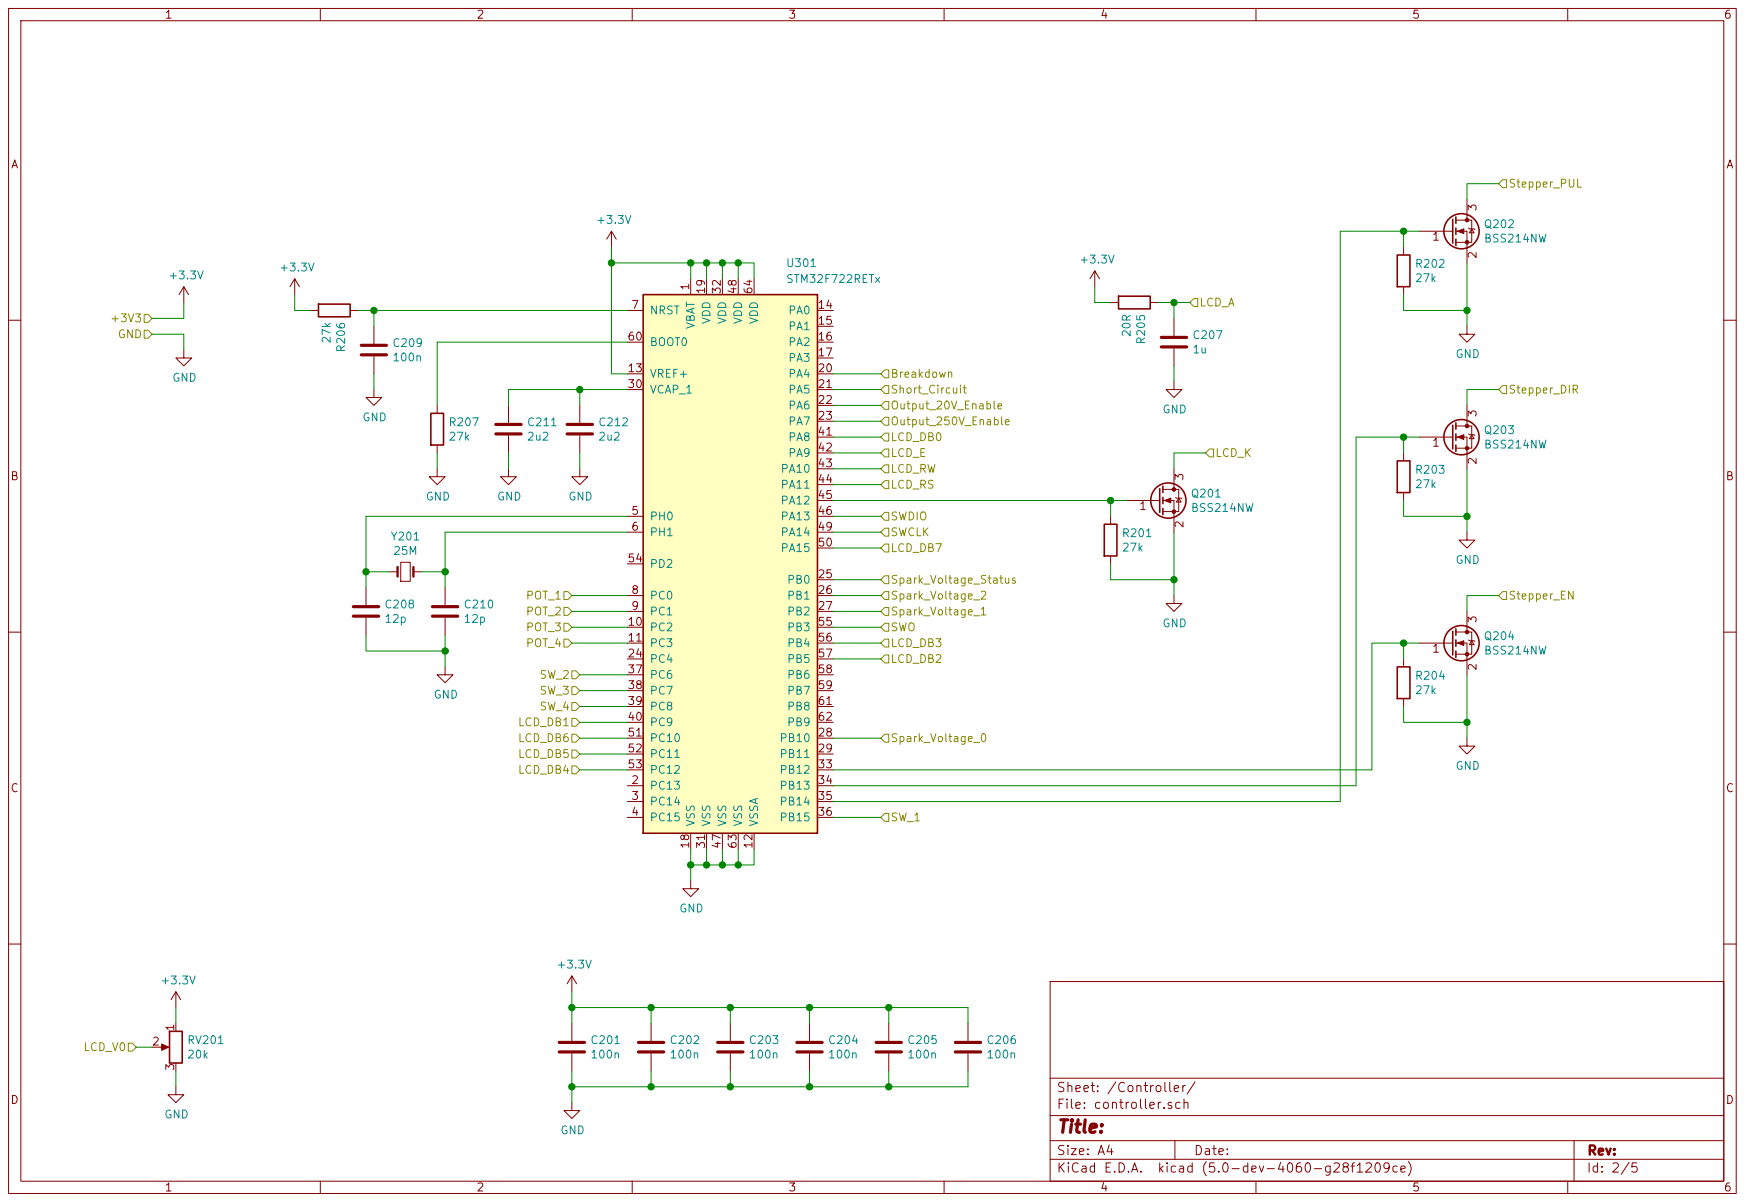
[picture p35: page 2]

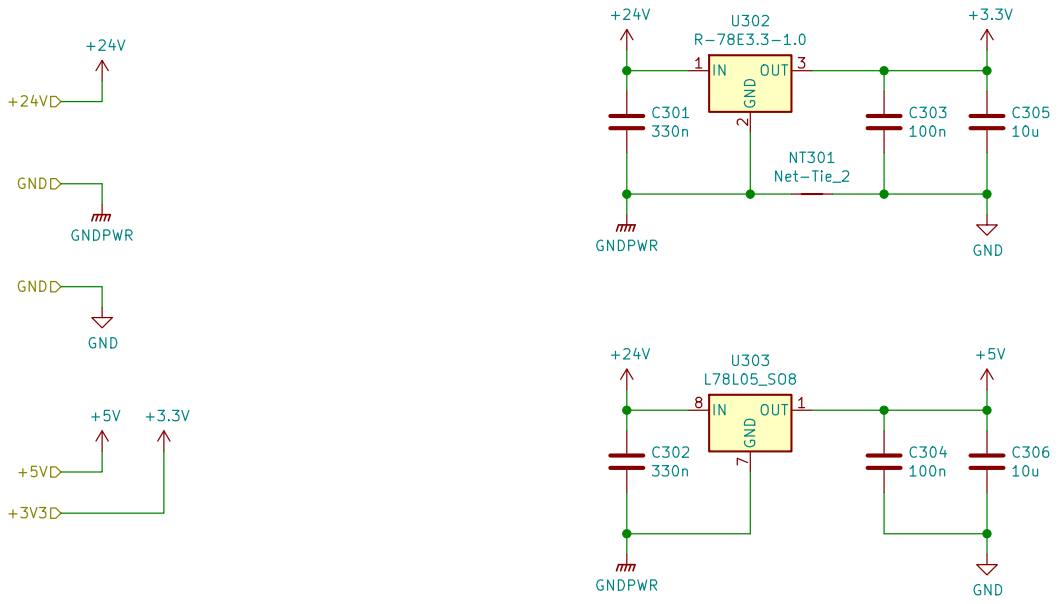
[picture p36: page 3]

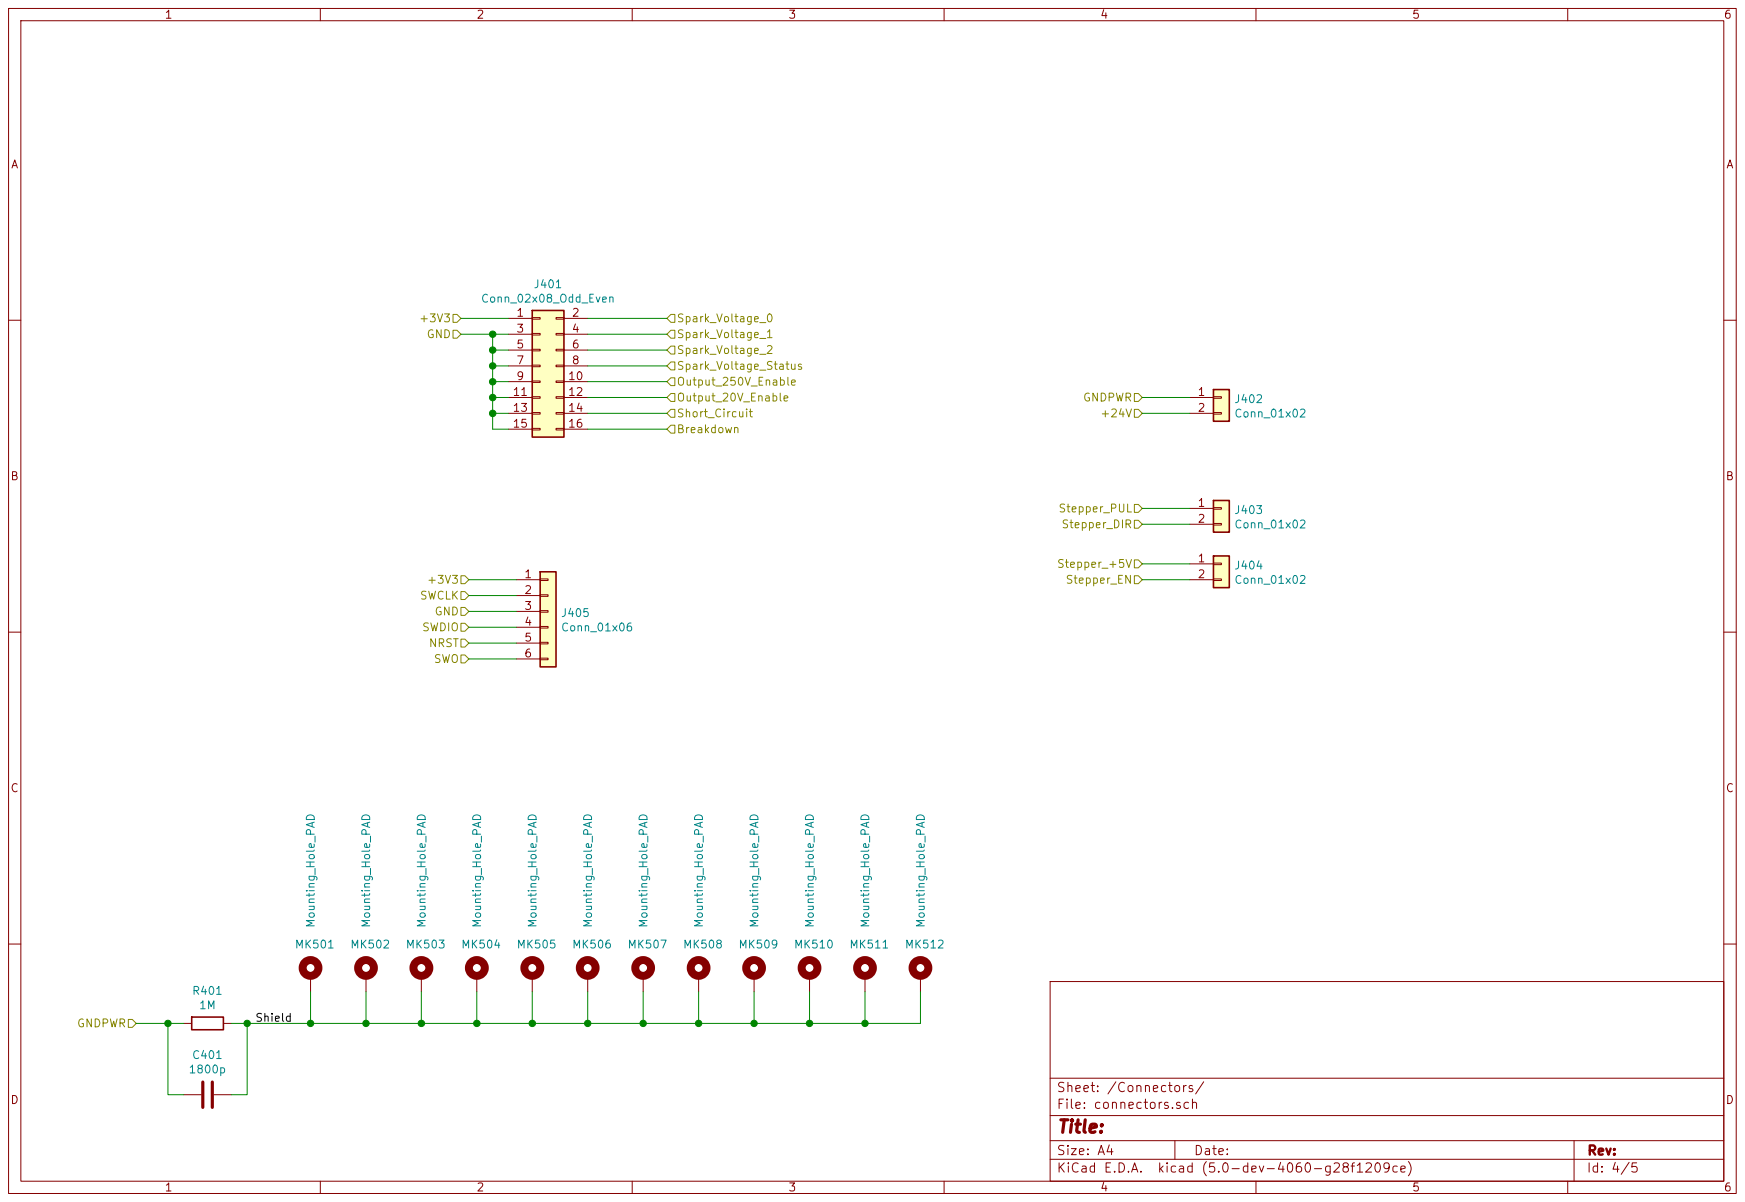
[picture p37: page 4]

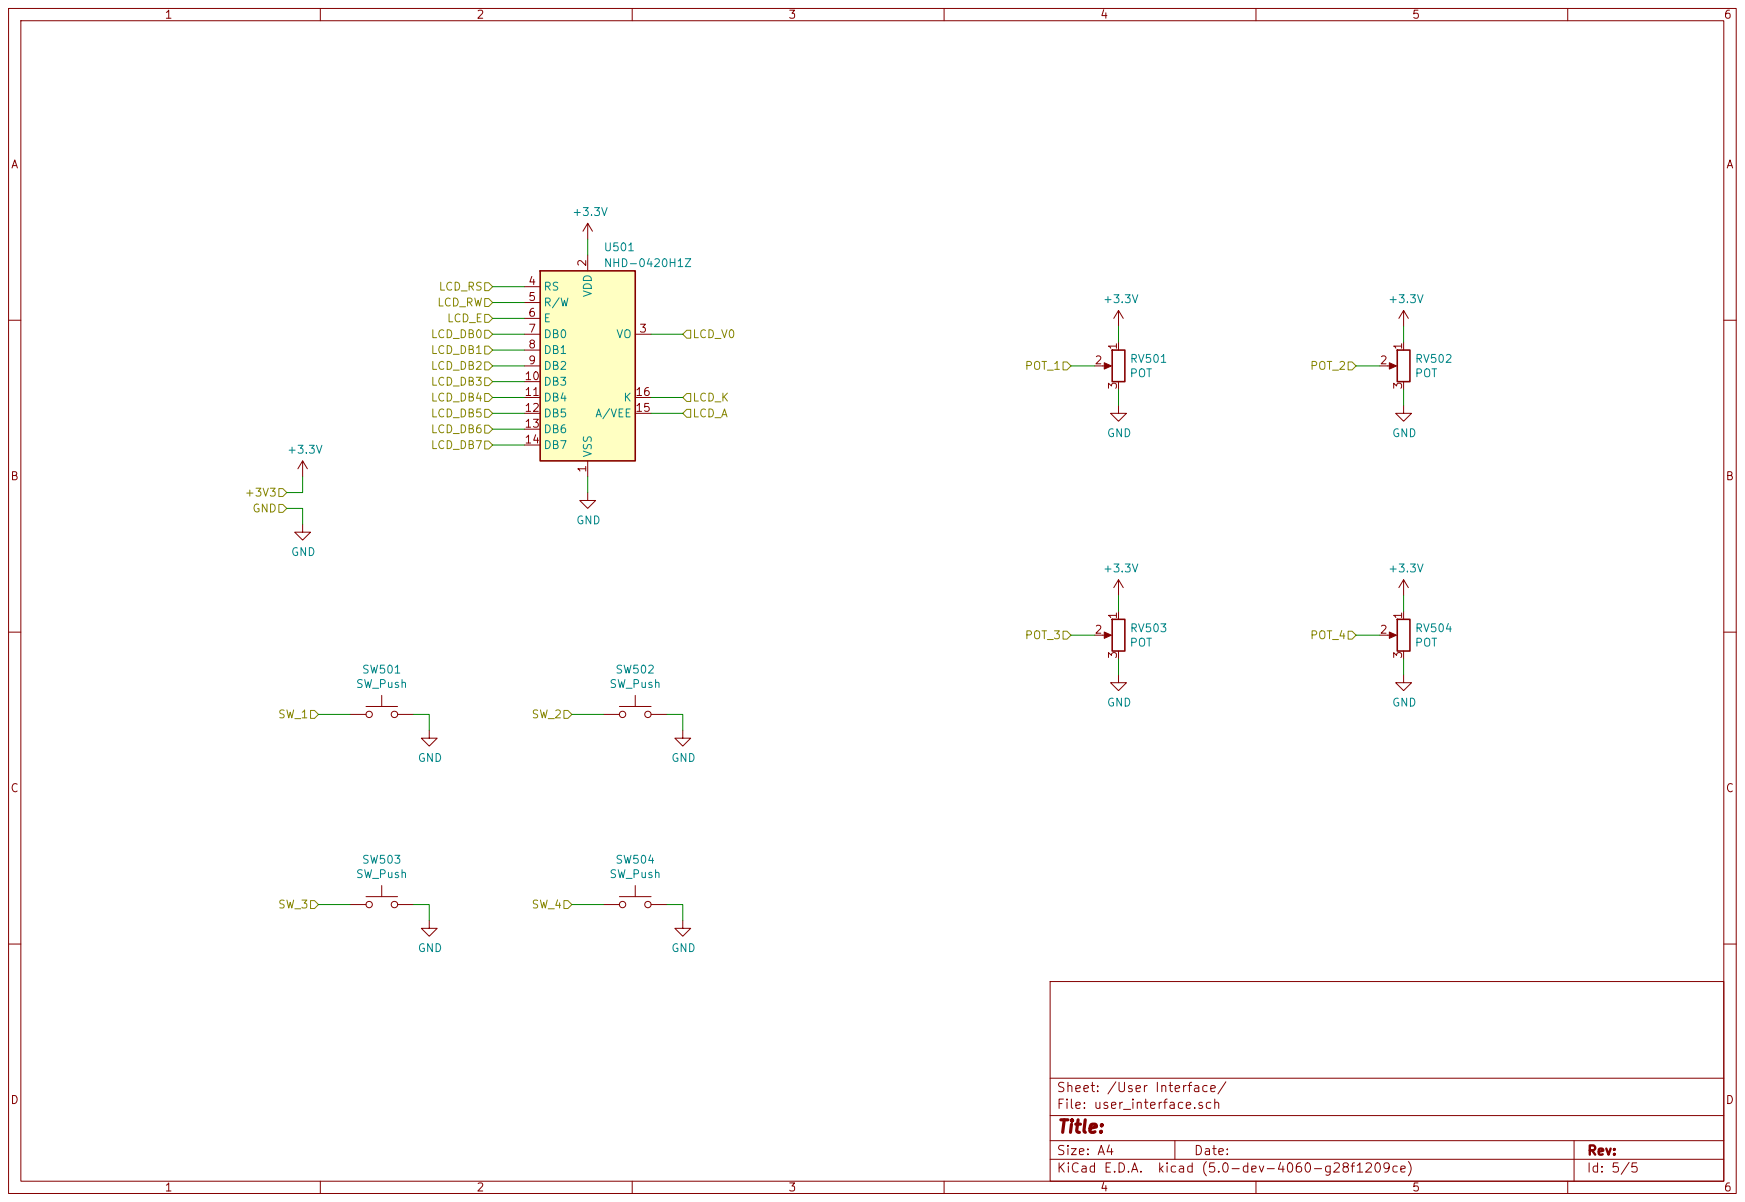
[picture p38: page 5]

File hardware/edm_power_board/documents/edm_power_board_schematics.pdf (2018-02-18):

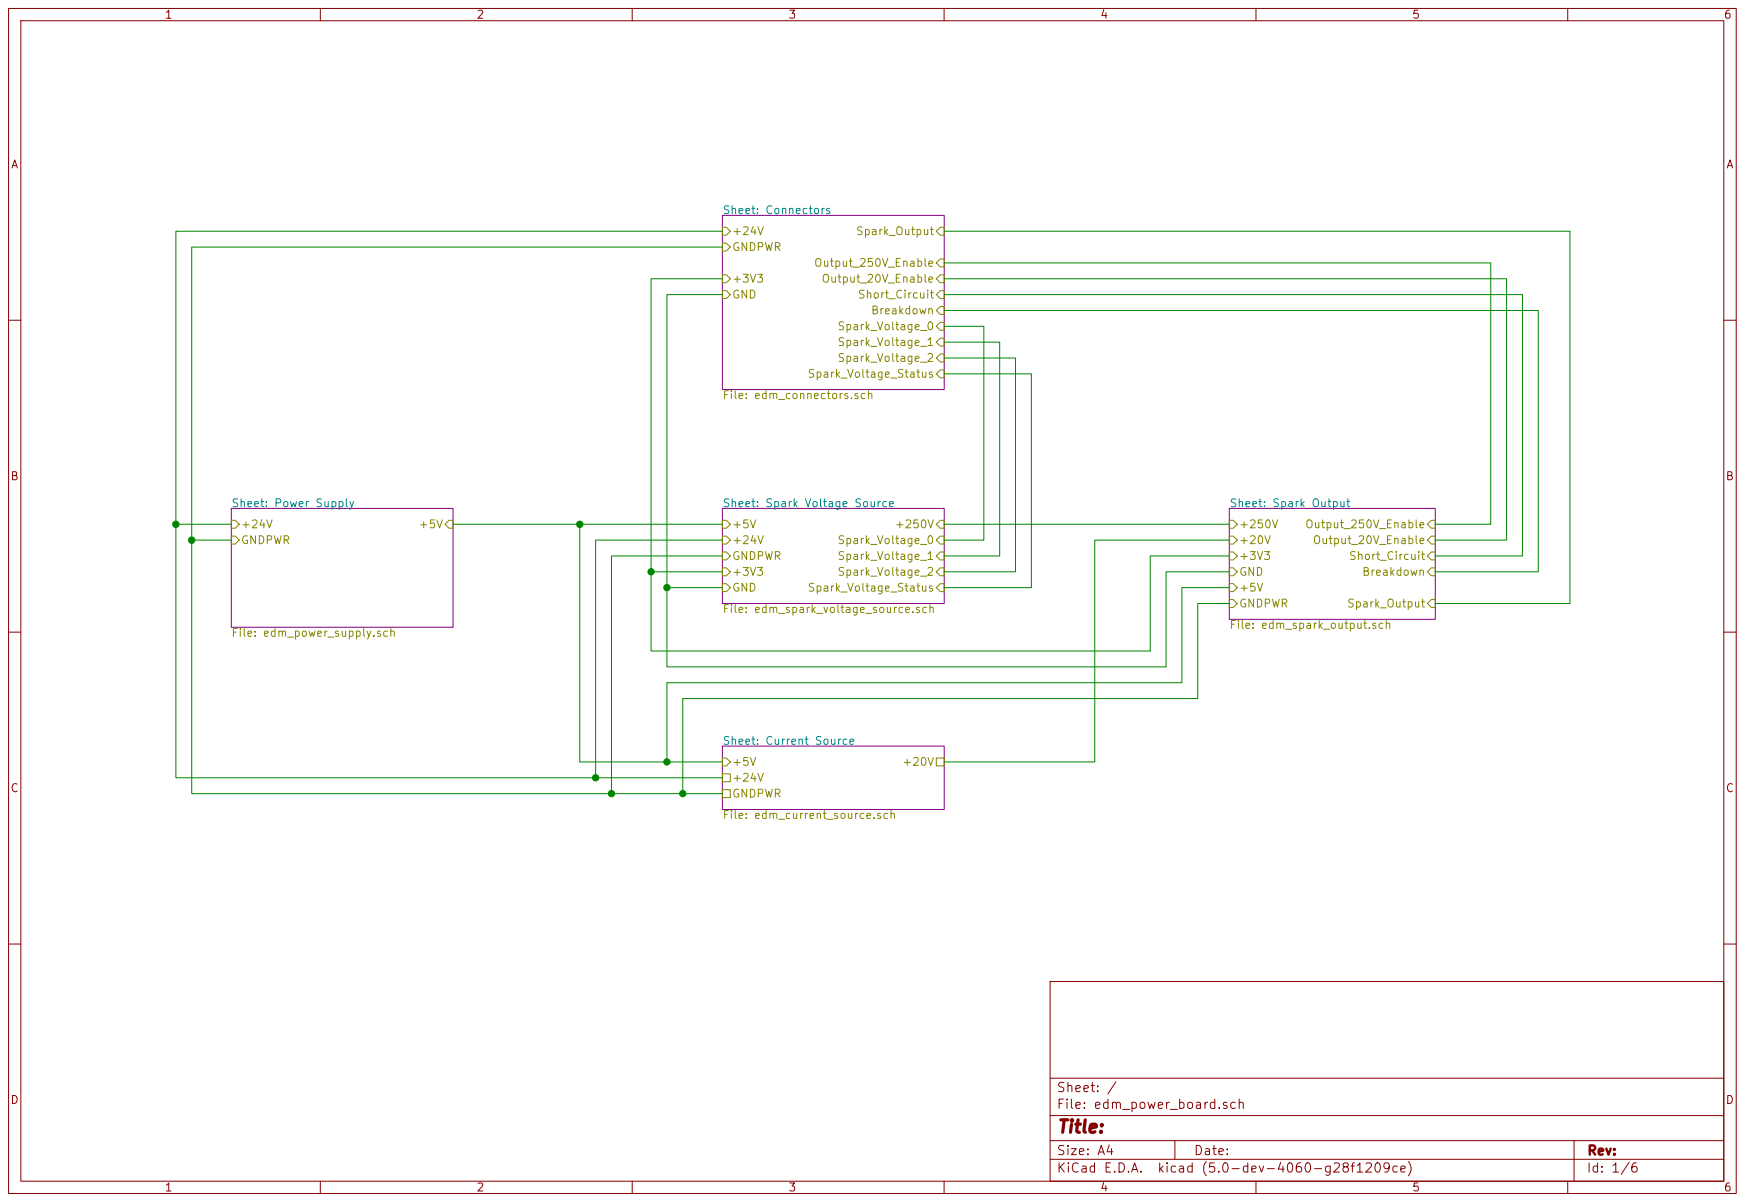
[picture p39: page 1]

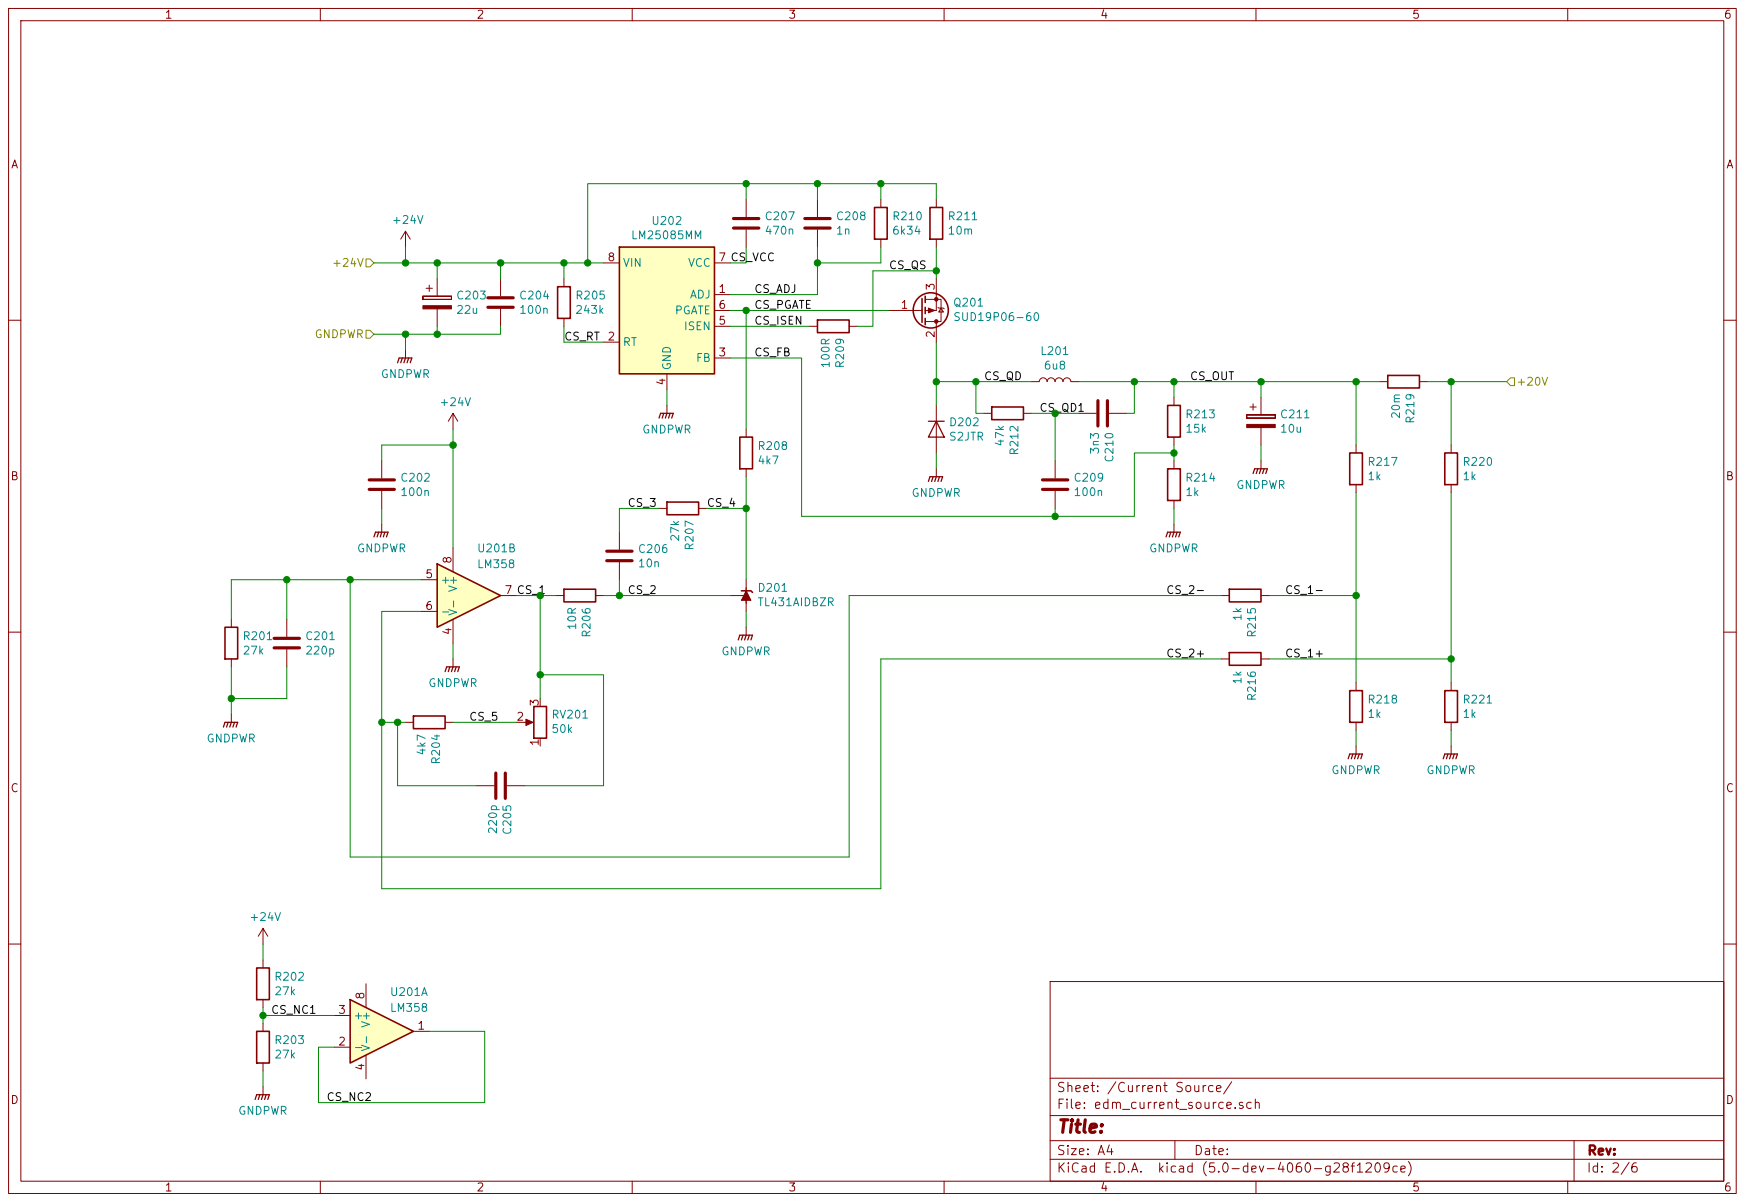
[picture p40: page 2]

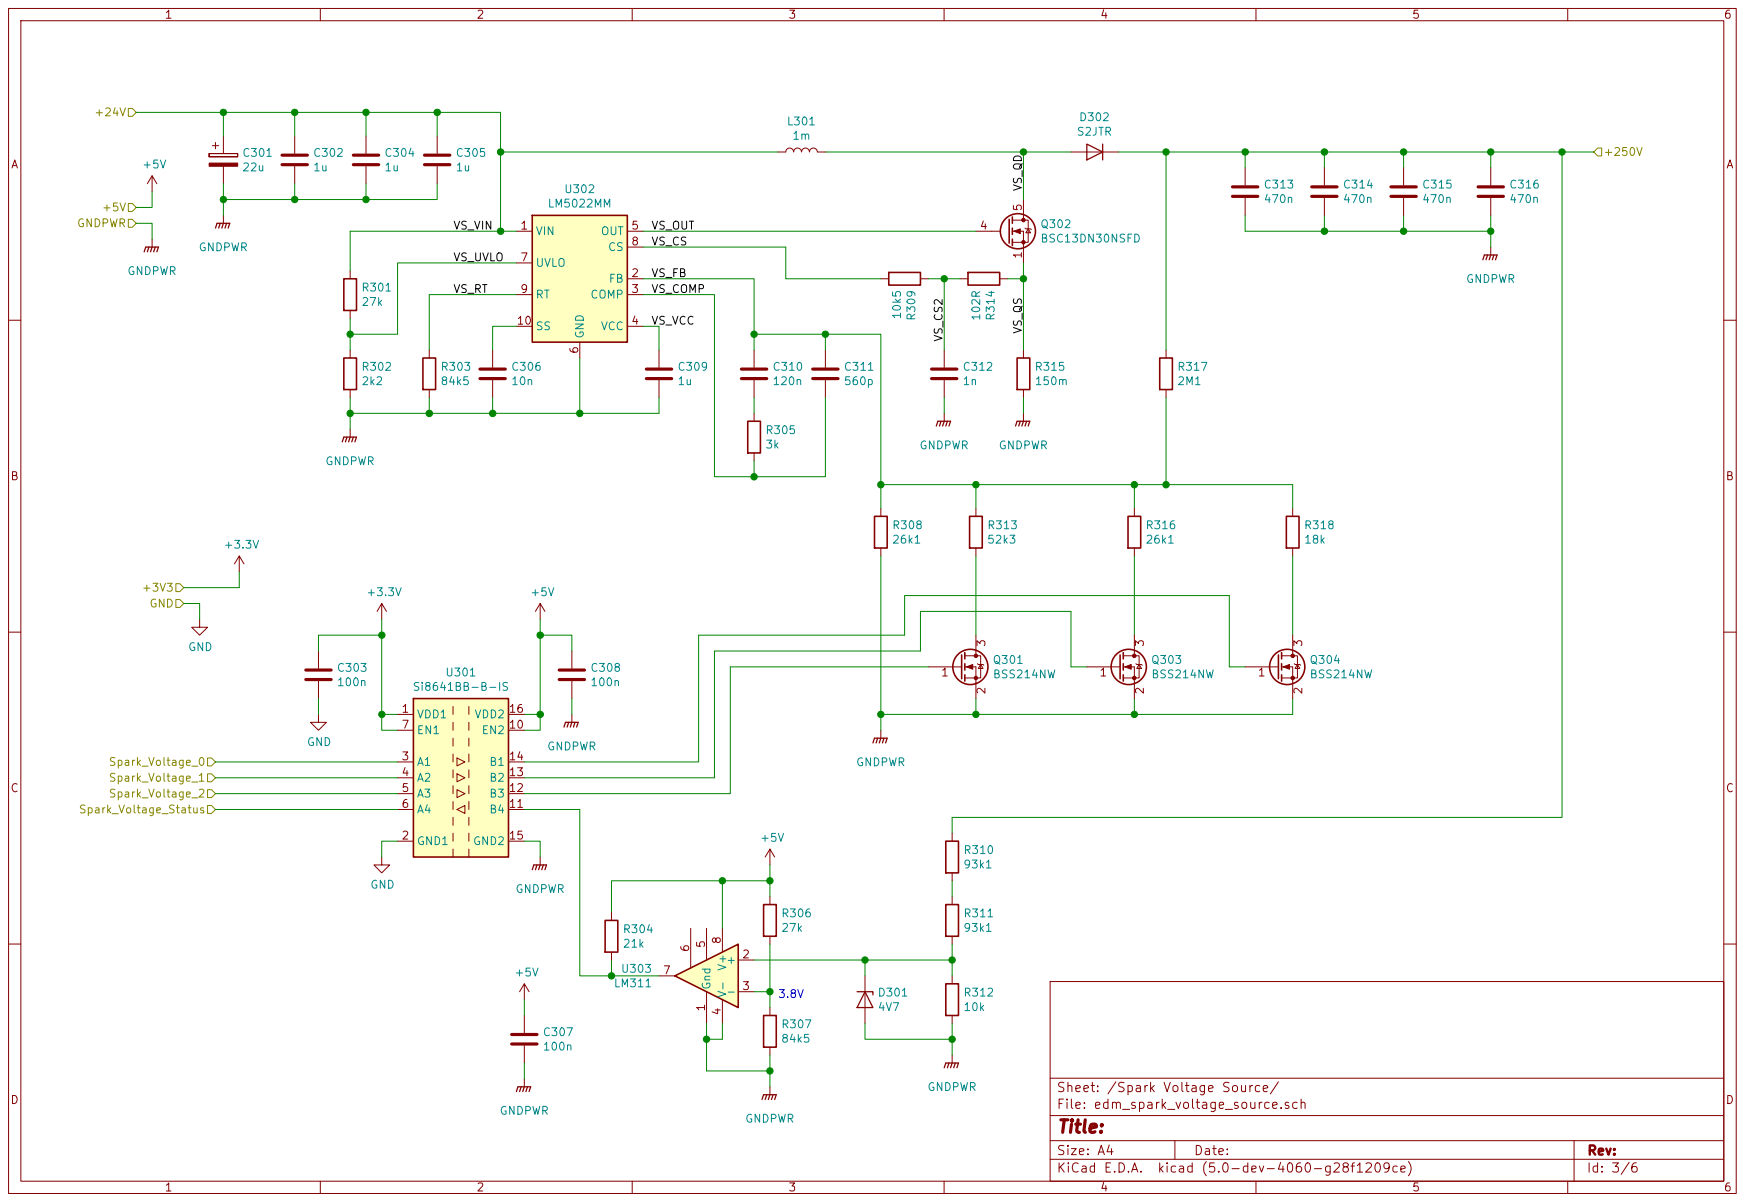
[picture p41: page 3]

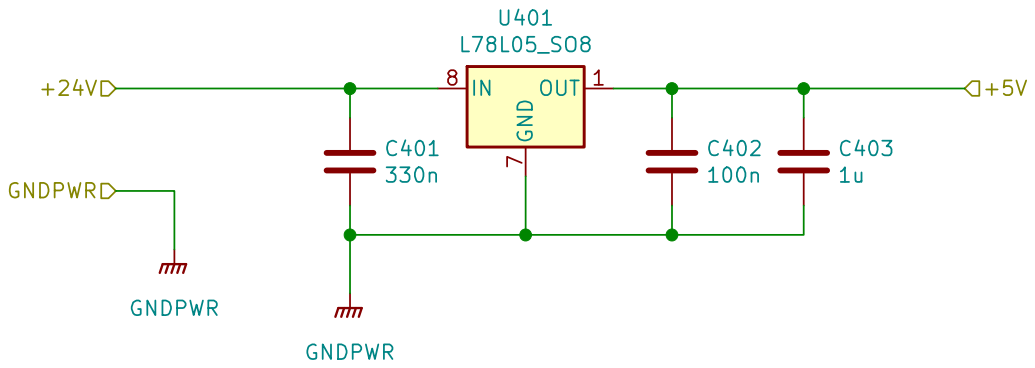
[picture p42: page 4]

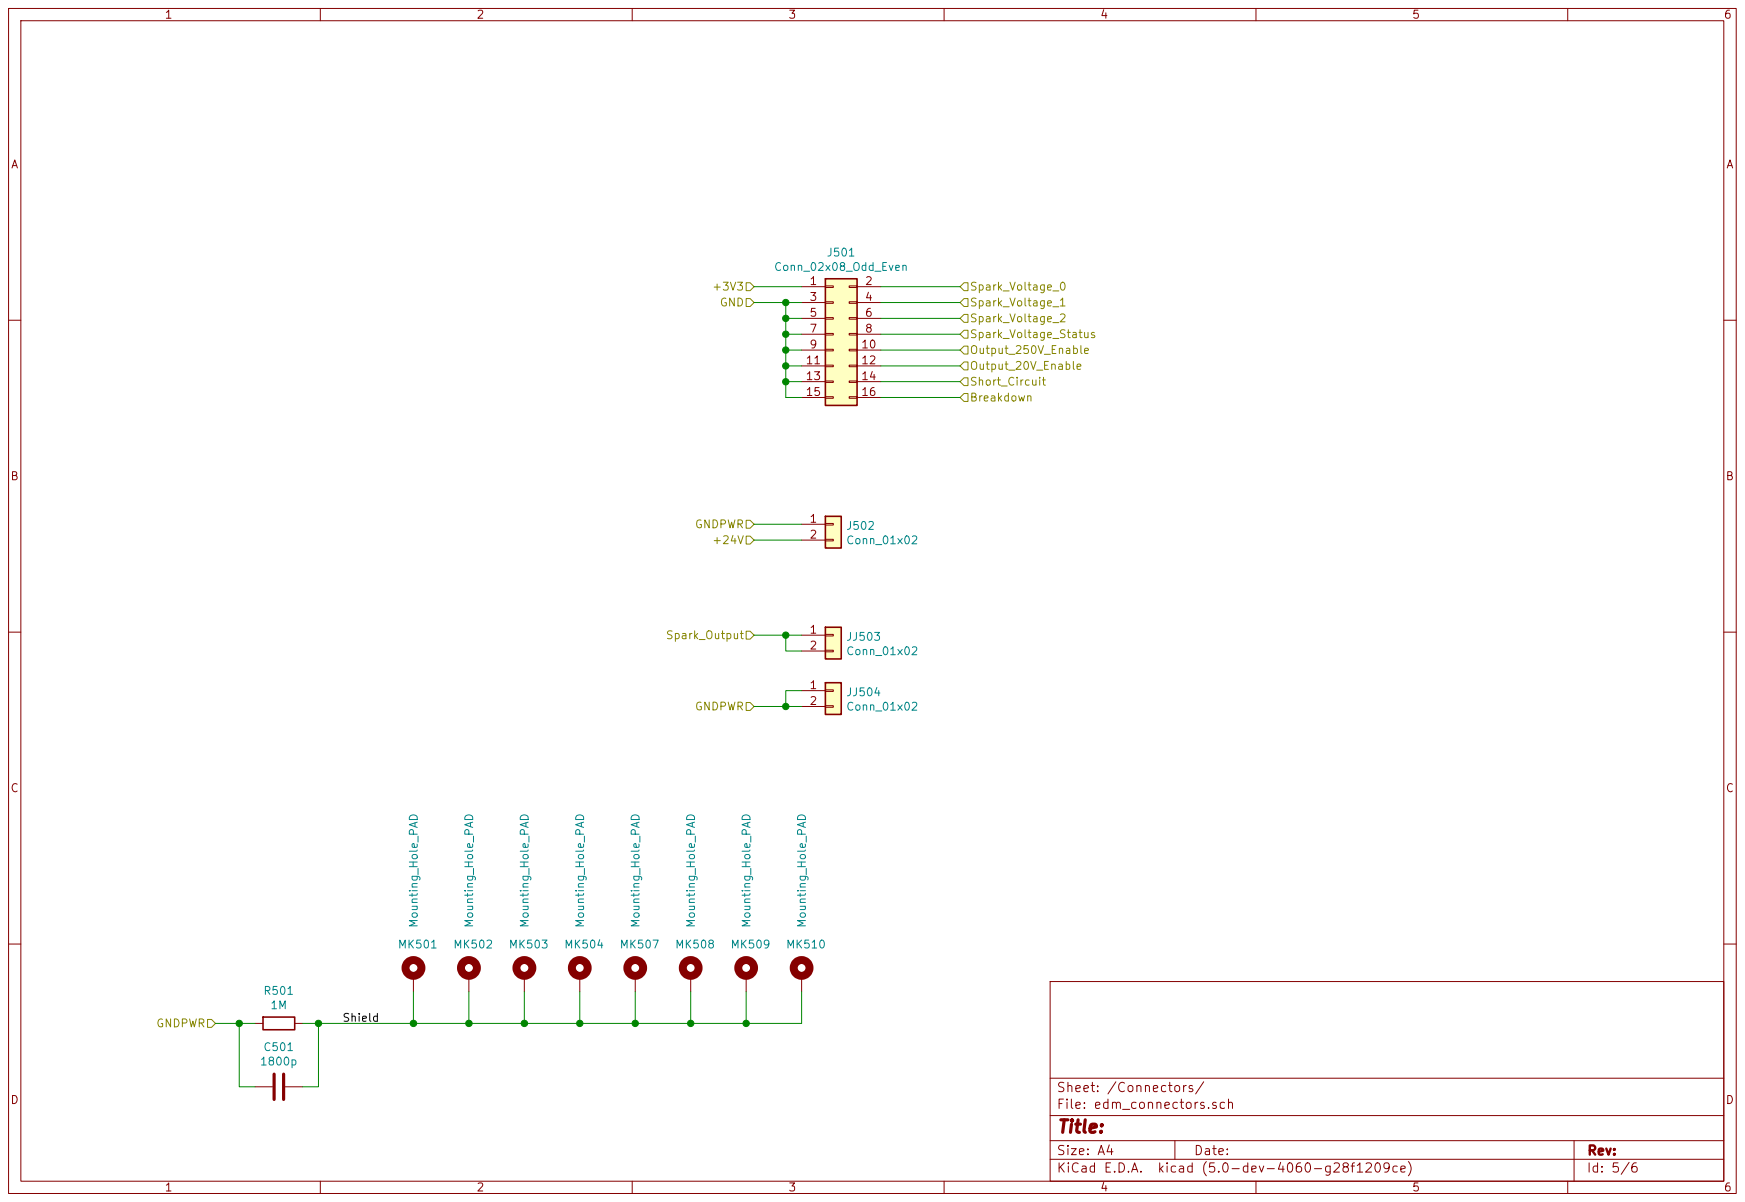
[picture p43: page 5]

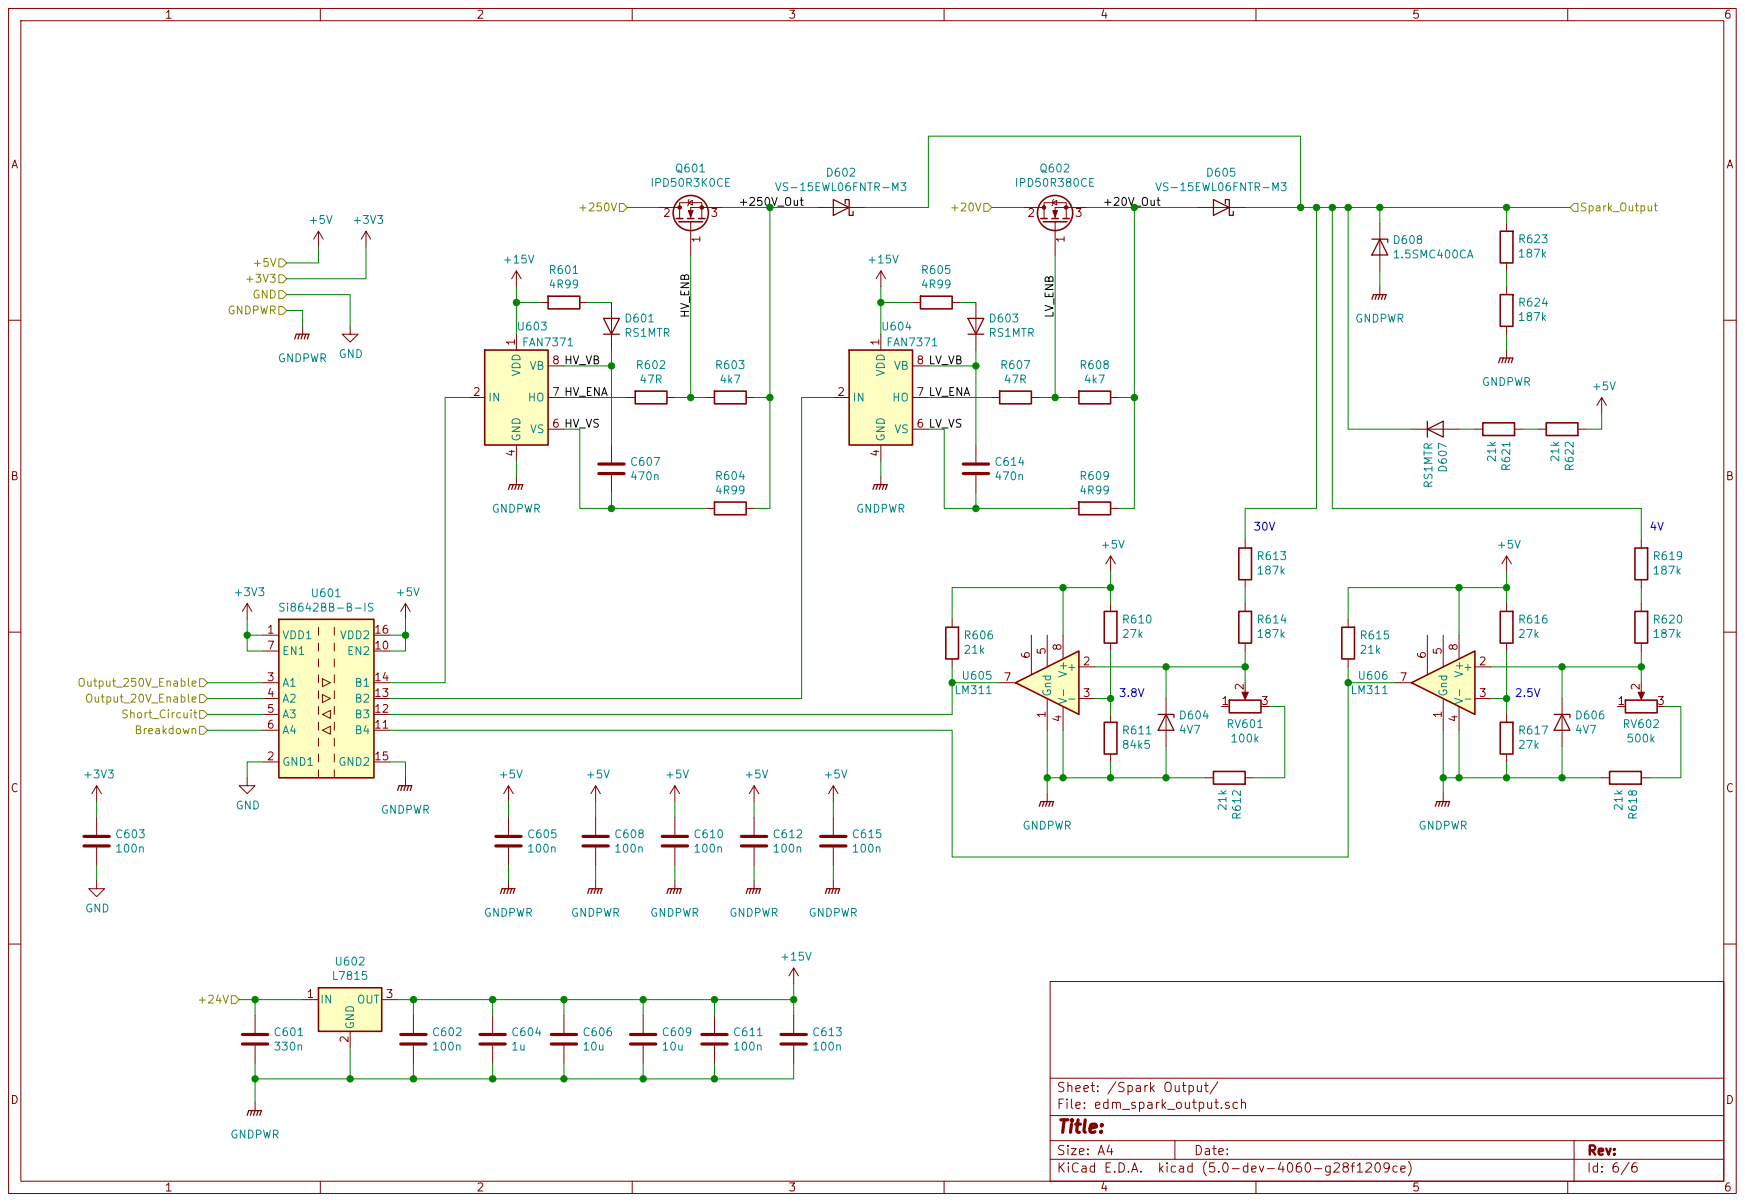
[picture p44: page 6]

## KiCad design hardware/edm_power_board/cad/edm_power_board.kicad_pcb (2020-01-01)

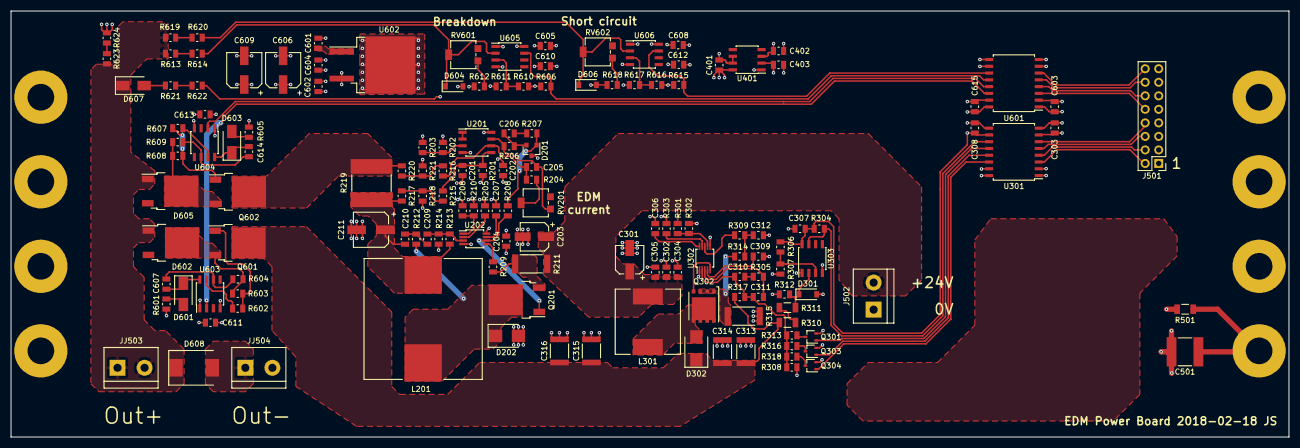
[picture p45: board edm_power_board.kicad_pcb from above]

Board: 4 copper layers, 240.0 x 80.0 mm, 158 parts (0 on the bottom side), 89 nets.

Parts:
C201, C205: 220p; R_0805_2012Metric
C202, C204, C209, C303, C307, C308, C402, C602, C603, C605, C608, C610, C611, C612, C613, C615: 100n; C_0805_2012Metric
C203, C301: 22u; CP_Elec_5x5.3
C206, C306: 10n; C_0805_2012Metric
C207, C607, C614: 470n; C_0805_2012Metric
C208, C312: 1n; C_0805_2012Metric
C210: 3n3; C_0805_2012Metric
C211, C606, C609: 10u; CP_Elec_6.3x5.3
C302, C304, C305, C309, C403, C604: 1u; C_0805_2012Metric
C310: 120n; C_0805_2012Metric
C311: 560p; C_0805_2012Metric
C313, C314, C315, C316: 470n; C_1812_4532Metric
C401, C601: 330n; C_0805_2012Metric
C501: 1800p; C_2220_5650Metric
D201: TL431AIDBZR; SOT-23
D202, D302: S2JTR; D_SMB
D301, D604, D606: 4V7; D_SOD-123
D601, D603, D607: RS1MTR; D_SMA
D602, D605: VS-15EWL06FNTR-M3; TO-252-2
D608: 1.5SMC400CA; D_SMC
J501: Conn_02x08_Odd_Even; PinHeader_2x08_P2.54mm_Vertical
J502: Conn_01x02; TerminalBlock_bornier-2_P5.08mm
JJ503, JJ504: Conn_01x02; TerminalBlock_bornier-2_P5.08mm
L201: 6u8; L_Wuerth_HCI-2212
L301: 1m; L_Pulse_PA4320
MK501, MK502, MK503, MK504, MK507, MK508, MK509, MK510: Mounting_Hole_PAD; MountingHole_5mm_Pad
Q201: SUD19P06-60; TO-252-2
Q301, Q303, Q304: BSS214NW; SOT-323_SC-70
Q302: BSC13DN30NSFD; TDSON-8-1
Q601: IPD50R3K0CE; TO-252-2
Q602: IPD50R380CE; TO-252-2
R201, R202, R203, R207, R301, R306, R610, R616, R617: 27k; R_0805_2012Metric
R204, R208, R603, R608: 4k7; R_0805_2012Metric
R205: 243k; R_0805_2012Metric
R206: 10R; R_0805_2012Metric
R209: 100R; R_0805_2012Metric
R210: 6k34; R_0805_2012Metric
R211: 10m; R_2512_6332Metric
R212: 47k; R_0805_2012Metric
R213: 15k; R_0805_2012Metric
R214, R215, R216, R217, R218, R220, R221: 1k; R_0805_2012Metric
R219: 20m; R_Stackpole_CSSH2728_4-100m
R302: 2k2; R_0805_2012Metric
R303, R307, R611: 84k5; R_0805_2012Metric
R304, R606, R612, R615, R618, R621, R622: 21k; R_0805_2012Metric
R305: 3k; R_0805_2012Metric
R308, R316: 26k1; R_0805_2012Metric
R309: 10k5; R_0805_2012Metric
R310, R311: 93k1; R_1206_3216Metric
R312: 10k; R_0805_2012Metric
R313: 52k3; R_0805_2012Metric
R314: 102R; R_0805_2012Metric
R315: 150m; R_2512_6332Metric
R317: 2M1; R_0805_2012Metric
R318: 18k; R_0805_2012Metric
R501: 1M; R_1206_3216Metric
R601, R604, R605, R609: 4R99; R_0805_2012Metric
R602, R607: 47R; R_0805_2012Metric
R613, R614, R619, R620, R623, R624: 187k; R_0805_2012Metric
RV201: 50k; Potentiometer_Bourns_3314G_Horizontal
RV601: 100k; Potentiometer_Bourns_3314G_Horizontal
RV602: 500k; Potentiometer_Bourns_3314G_Horizontal
U201: LM358; SOIC-8_3.9x4.9mm_P1.27mm
U202: LM25085MM; MSOP-8_3x3mm_P0.65mm
U301: Si8641BB-B-IS; SOIC-16W_7.5x10.3mm_P1.27mm
U302: LM5022MM; MSOP-10_3x3mm_P0.5mm
U303, U605, U606: LM311; SOIC-8_3.9x4.9mm_P1.27mm
U401: L78L05_SO8; SOIC-8_3.9x4.9mm_P1.27mm
U601: Si8642BB-B-IS; SOIC-16W_7.5x10.3mm_P1.27mm
U602: L7815; TO-263-2
U603, U604: FAN7371; SOIC-8_3.9x4.9mm_P1.27mm

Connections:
+3V3: C303.1, C603.1, J501.1, U301.1, U301.7, U601.1, U601.7
+5V: C307.1, C308.1, C402.1, C403.1, C605.1, C608.1, C610.1, C612.1, C615.1, R304.1, R306.1, R606.2, R610.2, R615.2, R616.2, R622.2, U301.10, U301.16, U303.8, U401.1, U601.10, U601.16, U605.8, U606.8
+15V: C602.1, C604.1, C606.1, C609.1, C611.1, C613.1, R601.2, R605.2, U602.3, U603.1, U604.1
+24V: C202.1, C203.1, C204.1, C207.1, C208.1, C301.1, C302.1, C304.1, C305.1, C401.1, J502.2, L301.1, R202.1, R205.1, R210.1, R211.1, R301.1, U201.8, U202.8, U302.1, U401.8
/Connectors/Breakdown: J501.16, U601.6
/Connectors/Output_20V_Enable: J501.12, U601.4
/Connectors/Output_250V_Enable: J501.10, U601.3
/Connectors/Shield: C501.1, MK501.1, MK502.1, MK503.1, MK504.1, MK507.1, MK508.1, MK509.1, MK510.1, R501.1
/Connectors/Short_Circuit: J501.14, U601.5
/Connectors/Spark_Output: D602.1, D605.1, D607.1, D608.1, JJ503.1, JJ503.2, R613.2, R619.2, R623.2
/Connectors/Spark_Voltage_0: J501.2, U301.3
/Connectors/Spark_Voltage_1: J501.4, U301.4
/Connectors/Spark_Voltage_2: J501.6, U301.5
/Connectors/Spark_Voltage_Status: J501.8, U301.6
/Current Source/+20V: Q602.2, R219.1, R220.1
/Current Source/CS_1: C205.1, R206.2, RV201.3, U201.7
/Current Source/CS_1+: R216.1, R220.2, R221.1
/Current Source/CS_1-: R215.1, R217.2, R218.1
/Current Source/CS_2: C206.2, D201.2, R206.1
/Current Source/CS_2+: C205.2, R204.2, R216.2, U201.6
/Current Source/CS_2-: C201.1, R201.1, R215.2, U201.5
/Current Source/CS_3: C206.1, R207.2
/Current Source/CS_4: D201.1, R207.1, R208.2
/Current Source/CS_5: R204.1, RV201.2
/Current Source/CS_ADJ: C208.2, R210.2, U202.1
/Current Source/CS_FB: C209.2, R213.2, R214.1, U202.3
/Current Source/CS_ISEN: R209.2, U202.5
/Current Source/CS_NC1: R202.2, R203.1, U201.3
/Current Source/CS_NC2: U201.1, U201.2
/Current Source/CS_OUT: C210.1, C211.1, L201.2, R213.1, R217.1, R219.2
/Current Source/CS_PGATE: Q201.1, R208.1, U202.6
/Current Source/CS_QD: D202.1, L201.1, Q201.2, R212.2
/Current Source/CS_QD1: C209.1, C210.2, R212.1
/Current Source/CS_QS: Q201.3, R209.1, R211.2
/Current Source/CS_RT: R205.2, U202.2
/Current Source/CS_VCC: C207.2, U202.7
/Spark Output/+20V_Out: D605.2, Q602.3, R608.1, R609.1
/Spark Output/+24V: C601.1, U602.1
/Spark Output/+250V: C313.1, C314.1, C315.1, C316.1, D302.1, Q601.2, R310.1, R317.1
/Spark Output/+250V_Out: D602.2, Q601.3, R603.1, R604.1
/Spark Output/HV_ENA: R602.2, U603.7
/Spark Output/HV_ENB: Q601.1, R602.1, R603.2
/Spark Output/HV_VB: C607.1, D601.1, U603.8
/Spark Output/HV_VS: C607.2, R604.2, U603.6
/Spark Output/LV_ENA: R607.2, U604.7
/Spark Output/LV_ENB: Q602.1, R607.1, R608.2
/Spark Output/LV_VB: C614.1, D603.1, U604.8
/Spark Output/LV_VS: C614.2, R609.2, U604.6
/Spark Voltage Source/VS_COMP: C311.2, R305.2, U302.3
/Spark Voltage Source/VS_CS: R309.2, U302.8
/Spark Voltage Source/VS_CS2: C312.1, R309.1, R314.2
/Spark Voltage Source/VS_FB: C310.1, C311.1, R308.1, R313.1, R316.1, R317.2, R318.1, U302.2
/Spark Voltage Source/VS_OUT: Q302.4, U302.5
/Spark Voltage Source/VS_QD: D302.2, L301.2, Q302.5
/Spark Voltage Source/VS_QS: Q302.1, Q302.2, Q302.3, R314.1, R315.1
/Spark Voltage Source/VS_RT: R303.1, U302.9
/Spark Voltage Source/VS_UVLO: R301.2, R302.1, U302.7
/Spark Voltage Source/VS_VCC: C309.1, U302.4
GND: C303.2, C603.2, J501.3, J501.5, J501.7, J501.9, J501.11, J501.13, J501.15, U301.2, U301.8, U601.2, U601.8
GNDPWR: C201.2, C202.2, C203.2, C204.2, C211.2, C301.2, C302.2, C304.2, C305.2, C306.2, C307.2, C308.2, C309.2, C312.2, C313.2, C314.2, C315.2, C316.2, C401.2, C402.2, C403.2, C501.2, C601.2, C602.2, C604.2, C605.2, C606.2, C608.2, C609.2, C610.2, C611.2, C612.2, C613.2, C615.2, D201.3, D202.2, D301.2, D604.2, D606.2, D608.2, J502.1, JJ504.1, JJ504.2, Q301.2, Q303.2, Q304.2, R201.2, R203.2, R214.2, R218.2, R221.2, R302.2, R303.2, R307.2, R308.2, R312.2, R315.2, R501.2, R611.1, R612.1, R617.1, R618.1, R624.1, U201.4, U202.4, U301.9, U301.15, U302.6, U303.1, U303.4, U401.2, U401.3, U401.6, U401.7, U601.9, U601.15, U602.2, U603.4, U604.4, U605.1, U605.4, U606.1, U606.4
unnamed: C306.1, U302.10
unnamed: C310.2, R305.1
unnamed: D301.1, R311.2, R312.1, U303.2
unnamed: D601.2, R601.1
unnamed: D603.2, R605.1
unnamed: D604.1, R614.1, RV601.2, U605.2
unnamed: D606.1, R620.1, RV602.2, U606.2
unnamed: D607.2, R621.1
unnamed: Q301.1, U301.12
unnamed: Q301.3, R313.2
unnamed: Q303.1, U301.13
unnamed: Q303.3, R316.2
unnamed: Q304.1, U301.14
unnamed: Q304.3, R318.2
unnamed: R304.2, U301.11, U303.7
unnamed: R306.2, R307.1, U303.3
unnamed: R310.2, R311.1
unnamed: R606.1, U601.12, U605.7
unnamed: R610.1, R611.2, U605.3
unnamed: R612.2, RV601.3
unnamed: R613.1, R614.2
unnamed: R615.1, U601.11, U606.7
unnamed: R616.1, R617.2, U606.3
unnamed: R618.2, RV602.3
unnamed: R619.1, R620.2
unnamed: R621.2, R622.1
unnamed: R623.1, R624.2
unnamed: U601.13, U604.2
unnamed: U601.14, U603.2

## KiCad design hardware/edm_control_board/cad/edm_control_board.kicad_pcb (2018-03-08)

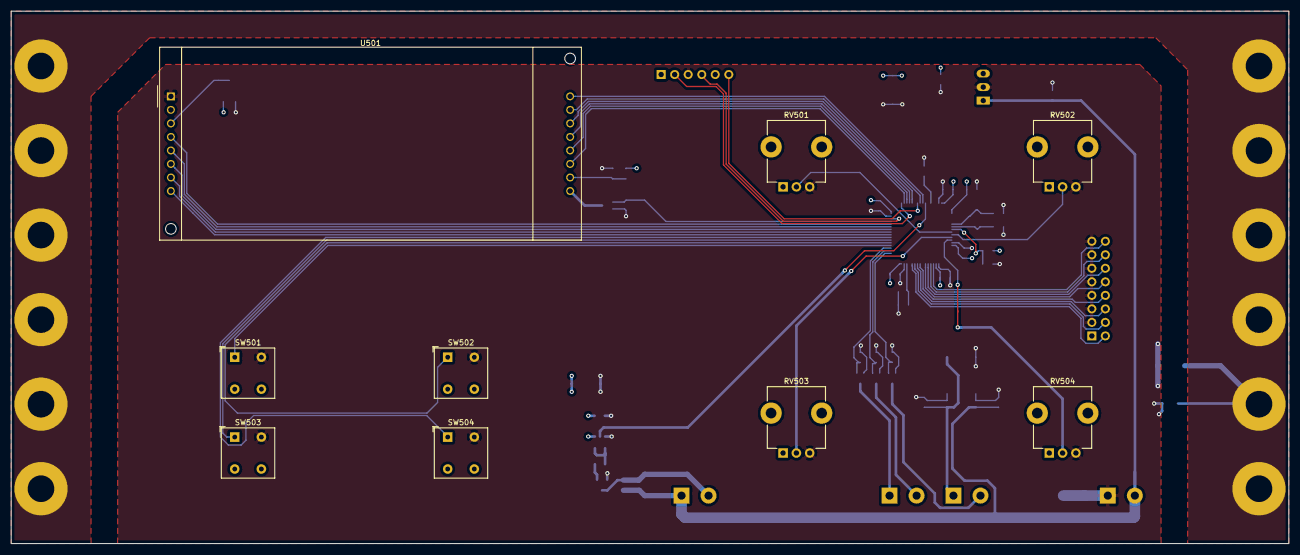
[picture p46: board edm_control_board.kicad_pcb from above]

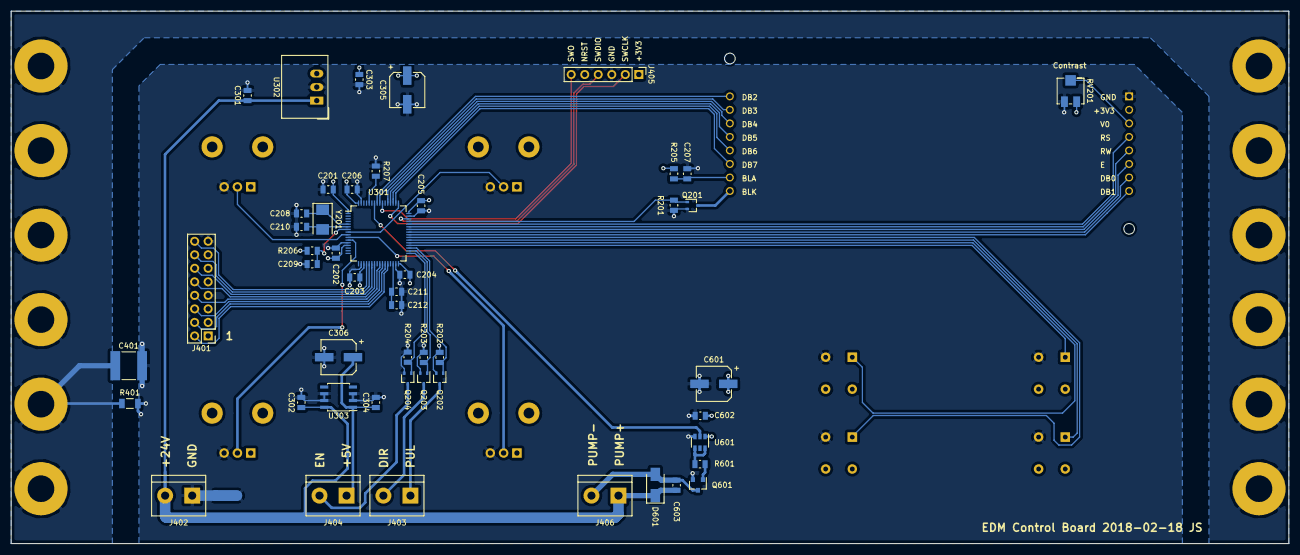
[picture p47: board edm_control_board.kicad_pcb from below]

Board: 4 copper layers, 240.0 x 100.0 mm, 71 parts (50 on the bottom side), 54 nets.

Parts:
C201, C202, C203, C204, C205, C206, C209, C303, C304, C602: 100n; C_0805_2012Metric
C207: 1u; C_0805_2012Metric
C208, C210: 12p; C_0805_2012Metric
C211, C212: 2u2; C_0805_2012Metric
C301, C302: 330n; C_0805_2012Metric
C305, C306, C601: 10u; CP_Elec_6.3x5.3
C401: 1800p; C_2220_5650Metric
C603: 1n; C_0805_2012Metric
D601: CDBA140-G; D_SMA
J401: Conn_02x08_Odd_Even; PinHeader_2x08_P2.54mm_Vertical
J402, J403, J404, J406: Conn_01x02; TerminalBlock_bornier-2_P5.08mm
J405: Conn_01x06; PinHeader_1x06_P2.54mm_Vertical
MK501, MK502, MK503, MK504, MK505, MK506, MK507, MK508, MK509, MK510, MK511, MK512: Mounting_Hole_PAD; MountingHole_5mm_Pad
NT301: Net-Tie_2; NetTie-2_SMD_Pad2.0mm
Q201, Q202, Q203, Q204: BSS214NW; SOT-323_SC-70
Q601: DMN3404L-7; SOT-23
R201, R202, R203, R204, R206, R207: 27k; R_0805_2012Metric
R205: 20R; R_0805_2012Metric
R401: 1M; R_1206_3216Metric
R601: 4R99; R_0805_2012Metric
RV201: 20k; Potentiometer_Bourns_3214J_Horizontal
RV501, RV502, RV503, RV504: POT; Potentiometer_TT_P0915N
SW501, SW502, SW503, SW504: SW_Push; SW_PUSH_CK_PVA1
U301: STM32F722RETx; LQFP-64_10x10mm_P0.5mm
U302: R-78E3.3-1.0; Converter_DCDC_RECOM_R-78E-0.5_THT
U303: L78L05_SO8; SOIC-8_3.9x4.9mm_P1.27mm
U501: NHD-0420H1Z
U601: ZXGD3009E6; SOT-23-6
Y201: 25M; Crystal_SMD_5032-2Pin_5.0x3.2mm

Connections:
+3V3: C201.1, C202.1, C203.1, C204.1, C205.1, C206.1, C303.1, C305.1, C601.1, C602.1, J401.1, J405.1, R205.2, R206.2, RV201.1, RV501.1, RV502.1, RV503.1, RV504.1, U301.1, U301.13, U301.19, U301.32, U301.48, U301.64, U302.3, U501.2, U601.1
+5V: C304.1, C306.1, J404.1, U303.1
+24V: C301.1, C302.1, C603.1, D601.1, J402.2, J406.1, U302.1, U303.8
/Connectors/Breakdown: J401.16, U301.20
/Connectors/Output_20V_Enable: J401.12, U301.22
/Connectors/Output_250V_Enable: J401.10, U301.23
/Connectors/SWCLK: J405.2, U301.49
/Connectors/SWDIO: J405.4, U301.46
/Connectors/SWO: J405.6, U301.55
/Connectors/Shield: C401.1, MK501.1, MK502.1, MK503.1, MK504.1, MK505.1, MK506.1, MK507.1, MK508.1, MK509.1, MK510.1, MK511.1, MK512.1, R401.1
/Connectors/Short_Circuit: J401.14, U301.21
/Connectors/Spark_Voltage_0: J401.2, U301.28
/Connectors/Spark_Voltage_1: J401.4, U301.27
/Connectors/Spark_Voltage_2: J401.6, U301.26
/Connectors/Spark_Voltage_Status: J401.8, U301.25
/Connectors/Stepper_DIR: J403.2, Q203.3
/Connectors/Stepper_EN: J404.2, Q204.3
/Connectors/Stepper_PUL: J403.1, Q202.3
/Connectors/Water_Pump_NEG: C603.2, D601.2, J406.2, Q601.3
/Controller/LCD_A: C207.1, R205.1, U501.15
/Controller/LCD_DB0: U301.41, U501.7
/Controller/LCD_DB1: U301.40, U501.8
/Controller/LCD_DB2: U301.57, U501.9
/Controller/LCD_DB3: U301.56, U501.10
/Controller/LCD_DB4: U301.53, U501.11
/Controller/LCD_DB5: U301.52, U501.12
/Controller/LCD_DB6: U301.51, U501.13
/Controller/LCD_DB7: U301.50, U501.14
/Controller/LCD_E: U301.42, U501.6
/Controller/LCD_K: Q201.3, U501.16
/Controller/LCD_RS: U301.44, U501.4
/Controller/LCD_RW: U301.43, U501.5
/Controller/LCD_V0: RV201.2, U501.3
/Controller/POT_1: RV501.2, U301.8
/Controller/POT_2: RV502.2, U301.9
/Controller/POT_3: RV503.2, U301.10
/Controller/POT_4: RV504.2, U301.11
/Controller/SW_1: SW501.1, U301.36
/Controller/SW_2: SW502.1, U301.37
/Controller/SW_3: SW503.1, U301.38
/Controller/SW_4: SW504.1, U301.39
/Controller/Water_Pump_PWM: U301.58, U601.2
GND: C201.2, C202.2, C203.2, C204.2, C205.2, C206.2, C207.2, C208.2, C209.2, C210.2, C211.2, C212.2, C301.2, C302.2, C303.2, C304.2, C305.2, C306.2, C401.2, C601.2, C602.2, J401.3, J401.5, J401.7, J401.9, J401.11, J401.13, J401.15, J402.1, J405.3, NT301.1, NT301.2, Q201.2, Q202.2, Q203.2, Q204.2, Q601.2, R201.2, R202.2, R203.2, R204.2, R207.2, R401.2, RV201.3, RV501.3, RV502.3, RV503.3, RV504.3, SW501.2, SW502.2, SW503.2, SW504.2, U301.12, U301.18, U301.31, U301.47, U301.63, U302.2, U303.2, U303.3, U303.6, U303.7, U501.1, U601.3
unnamed: C208.1, U301.5, Y201.1
unnamed: C209.1, R206.1, U301.7
unnamed: C210.1, U301.6, Y201.2
unnamed: C211.1, C212.1, U301.30
unnamed: Q201.1, R201.1, U301.45
unnamed: Q202.1, R202.1, U301.35
unnamed: Q203.1, R203.1, U301.34
unnamed: Q204.1, R204.1, U301.33
unnamed: Q601.1, R601.1
unnamed: R207.1, U301.60
unnamed: R601.2, U601.4, U601.6

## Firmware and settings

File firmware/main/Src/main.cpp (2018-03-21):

/**
 ******************************************************************************
 * @file           : main.c
 * @brief          : Main program body
 ******************************************************************************
 ** This notice applies to any and all portions of this file
 * that are not between comment pairs USER CODE BEGIN and
 * USER CODE END. Other portions of this file, whether
 * inserted by the user or by software development tools
 * are owned by their respective copyright owners.
 *
 * COPYRIGHT(c) 2018 STMicroelectronics
 *
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
 ******************************************************************************
 */
/* Includes ------------------------------------------------------------------*/
#include "main.h"
#include "stm32f7xx_hal.h"
#include "adc.h"
#include "tim.h"
#include "gpio.h"

#include "EdmState.h"
#include "Display.h"
#include "UserInput.h"
#include "WaterPump.h"
#include "StepperMotor.h"
#include "PowerBoard.h"


void SystemClock_Config(void);


extern "C" void initialise_monitor_handles(void);

/**
 * @brief  The application entry point.
 *
 * @retval None
 */
int main(void)
{
    /* Enable I-Cache-------------------------------------------------------------*/
    SCB_EnableICache();

    /* Enable D-Cache-------------------------------------------------------------*/
    SCB_EnableDCache();

    /* Reset of all peripherals, Initializes the Flash interface and the Systick. */
    HAL_Init();

    /* Configure the system clock */
    SystemClock_Config();

    /* Initialize all configured peripherals */
    MX_GPIO_Init();
    MX_ADC1_Init();
    MX_TIM4_Init();
    MX_TIM9_Init();
    MX_TIM12_Init();

    EdmState edm_state;
    Display display(&edm_state);
    UserInput user_input(&edm_state);
    StepperMotor stepper_motor(&edm_state);
    WaterPump water_pump(&edm_state);
    PowerBoard power_board(&edm_state);

    uint32_t tick_timeout = 0;

    //initialise_monitor_handles();

    /* Infinite loop */
    while (1)
    {

        if (HAL_GetTick() > 4000000000) {
            // Restart mcu before tick overflows
            // Future improvement: increase tick size to 64 bits
            NVIC_SystemReset();
        }


        if (HAL_GetTick() > tick_timeout) {

            //edm_state.hit_miss += 0.1;
            //if (edm_state.hit_miss > 1) edm_state.hit_miss = 0;

            edm_state.depth += 0.01;
            if (edm_state.depth > edm_state.depth_max) edm_state.depth = 0;


            tick_timeout += 38;
        }

        user_input.work();
        edm_state.work();
        water_pump.work();
        stepper_motor.work();
        power_board.work();
        display.work();

    }
}

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


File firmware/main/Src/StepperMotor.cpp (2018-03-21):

/*
 * StepperMotor.cpp
 *
 *  Created on: 8 mars 2018
 *      Author: JST
 */

#include "StepperMotor.h"

#include "stm32f7xx_hal.h"
#include "tim.h"

StepperMotor::StepperMotor(EdmState *_edm_state) {
    edm_state = _edm_state;
    previous_work_state = edm_state->work_state;

    HAL_GPIO_WritePin(GPIOB, Stepper_EN_Pin, GPIO_PIN_SET);
    HAL_GPIO_WritePin(GPIOB, Stepper_DIR_Pin, GPIO_PIN_RESET);

    HAL_TIM_PWM_Stop(&htim12, TIM_CHANNEL_1);
}

StepperMotor::~StepperMotor() {
    htim12.Instance->CCR1 = 0;
}

void StepperMotor::setDirection(Direction direction) {
    if (direction == Direction::UP) {
        HAL_GPIO_WritePin(GPIOB, Stepper_DIR_Pin, GPIO_PIN_SET);
    } else {
        HAL_GPIO_WritePin(GPIOB, Stepper_DIR_Pin, GPIO_PIN_RESET);
    }
}

void StepperMotor::setSpeed(uint32_t speed) {
    if (speed == 0) {
        HAL_GPIO_WritePin(GPIOB, Stepper_EN_Pin, GPIO_PIN_SET);

    } else {
        htim12.Instance->ARR = speed;
        htim12.Instance->CCR1 = speed / 2;
        HAL_TIM_PWM_Start(&htim12, TIM_CHANNEL_1);
        HAL_GPIO_WritePin(GPIOB, Stepper_EN_Pin, GPIO_PIN_RESET);
    }
}

void StepperMotor::work(void) {


    //edm_state->work_state = EdmWorkState::JOG_DOWN;

    /*
    if (edm_state->button_2_depressed) {
        state = State::JOG_UP;
    } else if (edm_state->button_4_depressed) {
        state = State::JOG_DOWN;
    } else {
        state = State::IDLE;
    }
    */

    if (edm_state->work_state != previous_work_state) {
        HAL_TIM_PWM_Stop(&htim12, TIM_CHANNEL_1);
        if (edm_state->work_state == EdmWorkState::IDLE) {
            setSpeed(0);

        } else if (edm_state->work_state == EdmWorkState::JOG_UP) {
            setSpeed(150);
            setDirection(Direction::UP);

        } else if (edm_state->work_state == EdmWorkState::JOG_DOWN) {
            setSpeed(150);
            setDirection(Direction::DOWN);

        } else if (edm_state->work_state == EdmWorkState::FINDING) {
            setSpeed(150);
            setDirection(Direction::DOWN);

        } else if (edm_state->work_state == EdmWorkState::STOP_RETRACT ||
                   edm_state->work_state == EdmWorkState::STOP_RETRACTING) {
            setSpeed(150);
            setDirection(Direction::UP);

        } else if (edm_state->work_state == EdmWorkState::FINDING_RETRACTING) {
            setSpeed(150);
            setDirection(Direction::UP);

        }


        previous_work_state = edm_state->work_state;
        //previous_state = state;
    }

    /*
	if (edm_state->button_1_depressed) {
		buffer[76] = 'S';
	} else {
		buffer[76] = 'R';
	}


	unsigned int pulse;
	pulse = edm_state->water_pump_duty_cycle / 4 * htim12.Instance->ARR;
	if (pulse < 50) {
		pulse = 0;
	} else if (pulse > htim12.Instance->ARR - 50) {
		pulse = htim12.Instance->ARR;
	}
     */


}

/*
#define Stepper_EN_Pin GPIO_PIN_12
#define Stepper_EN_GPIO_Port GPIOB
#define Stepper_DIR_Pin GPIO_PIN_13
#define Stepper_DIR_GPIO_Port GPIOB
#define Stepper_PUL_Pin GPIO_PIN_14
#define Stepper_PUL_GPIO_Port GPIOB
 */

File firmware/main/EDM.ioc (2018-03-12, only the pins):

Mcu.UserName=STM32F722RCTx
PA10.GPIO_Label=LCD_RW
PA10.Signal=GPIO_Output
PA11.GPIO_Label=LCD_RS
PA11.Signal=GPIO_Output
PA12.GPIO_Label=LCD_Background_Illumination
PA12.Signal=GPIO_Output
PA13.Signal=SYS_JTMS-SWDIO
PA14.Signal=SYS_JTCK-SWCLK
PA15.GPIO_Label=LCD_DB7
PA15.Signal=GPIO_Output
PA4.GPIO_Label=EDM_Short_Circuit
PA4.Signal=GPIO_Input
PA5.GPIO_Label=EDM_Breakdown
PA5.Signal=GPIO_Input
PA6.GPIO_Label=EDM_Output_20V_Enable
PA6.Signal=GPIO_Output
PA7.GPIO_Label=EDM_Output_250V_Enable
PA7.Signal=GPIO_Output
PA8.GPIO_Label=LCD_DB0
PA8.Signal=GPIO_Output
PA9.GPIO_Label=LCD_E
PA9.Signal=GPIO_Output
PB0.GPIO_Label=EDM_Spark_Voltage_Status
PB0.Signal=GPIO_Input
PB1.GPIO_Label=EDM_Spark_Voltage_2
PB1.Signal=GPIO_Output
PB10.GPIO_Label=EDM_Spark_Voltage_0
PB10.Signal=GPIO_Output
PB12.GPIO_Label=Stepper_EN
PB12.Signal=GPIO_Output
PB13.GPIO_Label=Stepper_DIR
PB13.Signal=GPIO_Output
PB14.GPIO_Label=Stepper_PUL
PB14.Signal=S_TIM12_CH1
PB15.GPIO_Label=Button_1
PB15.Signal=GPIO_Input
PB2.GPIO_Label=EDM_Spark_Voltage_1
PB2.Signal=GPIO_Output
PB4.GPIO_Label=LCD_DB3
PB4.Signal=GPIO_Output
PB5.GPIO_Label=LCD_DB2
PB5.Signal=GPIO_Output
PB6.GPIO_Label=Water_Pump_PWM
PB6.Signal=S_TIM4_CH1
PC0.GPIO_Label=POT_1
PC0.Signal=ADCx_IN10
PC1.GPIO_Label=POT_2
PC1.Signal=ADCx_IN11
PC10.GPIO_Label=LCD_DB6
PC10.Signal=GPIO_Output
PC11.GPIO_Label=LCD_DB5
PC11.Signal=GPIO_Output
PC12.GPIO_Label=LCD_DB4
PC12.Signal=GPIO_Output
PC2.GPIO_Label=POT_3
PC2.Signal=ADCx_IN12
PC3.GPIO_Label=POT_4
PC3.Signal=ADCx_IN13
PC6.GPIO_Label=Button_2
PC6.Signal=GPIO_Input
PC7.GPIO_Label=Button_3
PC7.Signal=GPIO_Input
PC8.GPIO_Label=Button_4
PC8.Signal=GPIO_Input
PC9.GPIO_Label=LCD_DB1
PC9.Signal=GPIO_Output
PH0-OSC_IN.Signal=RCC_OSC_IN
PH1-OSC_OUT.Signal=RCC_OSC_OUT

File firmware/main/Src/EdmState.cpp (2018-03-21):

/*
 * State.cpp
 *
 *  Created on: 7 mars 2018
 *      Author: JST
 */

#include "EdmState.h"

#include "stm32f7xx_hal.h"

EdmState::EdmState() {
    hit_miss = 0.75;
    depth = 0.03;
    depth_max = 0.5;
    ton = 15;
    toff = 120;
    voltage = 100;
    water_pump_duty_cycle = 0;

    button_1_depressed = false;
    button_2_depressed = false;
    button_3_depressed = false;
    button_4_depressed = false;

    short_circuit = false;
    breakdown = false;
    spark_voltage_status = false;

    work_state = EdmWorkState::IDLE;
}

EdmState::~EdmState() {

}


void EdmState::work(void) {
    static uint32_t tick_timeout = 0;

    if (work_state == EdmWorkState::IDLE) {

        if (button_1_depressed) {
            tick_timeout = HAL_GetTick() + 4000;
            work_state = EdmWorkState::FINDING;

        } else if (button_2_depressed) {
            work_state = EdmWorkState::JOG_UP;

        } else if (button_3_depressed) {
            work_state = EdmWorkState::IDLE;

        } else if (button_4_depressed) {
            work_state = EdmWorkState::JOG_DOWN;
        }

    } else if (work_state == EdmWorkState::JOG_UP) {
        if (!button_2_depressed) {
            work_state = EdmWorkState::IDLE;

        }

    } else if (work_state == EdmWorkState::JOG_DOWN) {
        if (!button_4_depressed) {
            work_state = EdmWorkState::IDLE;

        }

    } else if (work_state == EdmWorkState::FINDING) {

        if (button_3_depressed || HAL_GetTick() >= tick_timeout) {
            work_state = EdmWorkState::STOP_RETRACT;
        }

    } else if (work_state == EdmWorkState::FINDING_RETRACT) {
        tick_timeout = HAL_GetTick() + 100;
        work_state = EdmWorkState::FINDING_RETRACTING;

    } else if (work_state == EdmWorkState::FINDING_RETRACTING) {
        if (HAL_GetTick() >= tick_timeout) {
            work_state = EdmWorkState::IDLE;
        }

    } else if (work_state == EdmWorkState::STOP_RETRACT) {
        tick_timeout = HAL_GetTick() + 500;
        work_state = EdmWorkState::STOP_RETRACTING;

    } else if (work_state == EdmWorkState::STOP_RETRACTING) {
        if (HAL_GetTick() >= tick_timeout) {
            work_state = EdmWorkState::IDLE;
        }

    }



}

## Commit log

2018-01-31 KiCAD project
    [edm_power_board.kicad_pcb, edm_power_board.sch]
2018-01-31 Low voltage source
    [low_voltage_source.sch]
2018-01-31 Current source
    [edm_current_source.sch, edm_power_board.sch, low_voltage_source.sch]
2018-02-01 Spark voltage source
    [edm_current_source.sch, edm_power_board.sch, edm_spark_voltage_source.sch]
2018-02-06 Spark output
    [edm_spark_output.sch, edm_spark_voltage_source.sch]
2018-02-08 Assign part numbers
    [edm_connectors.sch, edm_current_source.sch, edm_power_supply.sch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]
2018-02-08 Set component references
    [edm_connectors.sch, edm_spark_output.sch, edm_spark_voltage_source.sch]
2018-02-10 Set part numbers
    [edm_current_source.sch, edm_power_supply.sch, edm_spark_output.sch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]
2018-02-11 PCB Outline
    [edm_current_source.sch, edm_power_board.kicad_pcb, edm_power_supply.sch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]
2018-02-11 Add input capacitors to spark
    [edm_power_board.kicad_pcb, edm_power_supply.sch, edm_spark_output.sch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]
2018-02-11 Component placement 250V
    [edm_power_board.kicad_pcb, edm_spark_voltage_source.sch]
2018-02-11 Spark output connector
    [edm_connectors.sch, edm_power_board.kicad_pcb, edm_power_board.sch]
2018-02-11 Plated mounting holes
    [edm_connectors.sch, edm_current_source.sch, edm_power_board.kicad_pcb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]
2018-02-12 Component placement
    [edm_connectors.sch, edm_current_source.sch, edm_power_board.kicad_pcb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]
2018-02-12 Add 3D cad
    [06AK2D.SLDPRT, 0707248_01.SLDPRT, 1458G5.SLDPRT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]
2018-02-13 Move files
    [edm_connectors.sch, edm_current_source.sch, edm_power_board.kicad_pcb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]
2018-02-13 Add bleeder resistor, remove 25u capacitors
    [edm_connectors.sch, edm_current_source.sch, edm_spark_output.sch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]
2018-02-13 Update bleed resistor
    [edm_power_board.kicad_pcb, edm_spark_output.sch]
2018-02-16 Rotate board
    [edm_connectors.sch, edm_power_board.kicad_pcb]
2018-02-16 Control board
    [connectors.sch, controller.sch, edm_control_board.kicad_pcb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]
2018-02-17 Main sheet
    [controller.sch, edm_control_board.sch, user_interface.sch]
2018-02-17 Power supply
    [controller.sch, edm_control_board.kicad_pcb, edm_control_board.sch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]
2018-02-17 Change folder
    [connectors.sch, controller.sch, edm_control_board.kicad_pcb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]
2018-02-17 Change to horizontal trim pot
    [controller.sch, edm_control_board.kicad_pcb]
2018-02-17 Update pinout
    [controller.sch, edm_control_board.kicad_pcb]
2018-02-18 Add SWD connector
    [connectors.sch, controller.sch, edm_control_board.kicad_pcb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]
2018-02-18 Add Y capacitor
    [connectors.sch, edm_control_board.kicad_pcb, edm_control_board.sch]
2018-02-18 3D files
    [06AK2D.STEP, 1458G5.SLDPRT, COM-10002.SLDPRT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]
2018-02-18 Add pdf schematics
2018-02-19 Add water pump output
    [connectors.sch, controller.sch, edm_control_board.sch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]
2018-02-19 Add water pump to pcb
    [edm_control_board.kicad_pcb]
2018-02-19 Added copper planes to front and back. Added gerber files.
    [edm_control_board.kicad_pcb, edm_power_board.kicad_pcb]
2018-02-20 Add BOM
    [controller.sch, edm_bom.xlsx, edm_control_board_bom.xlsx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]
2018-02-25 EDM Machine 3D CAD
    [edm_machine.SLDASM, linear_bearing_lwl9_bcs.SLDPRT, linear_rail_lwl9_bcs_160mm.SLDPRT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]
2018-02-25 EDM Control Box 3D CAD
    [06AK2D.SLDPRT, 1458G5.SLDPRT, COM-10002.SLDPRT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]
2018-02-25 Add screw M3 12mm
    [screw_m3_12.SLDPRT]
2018-02-25 Remove old files
    [06AK2D.SLDPRT, 06AK2D.STEP, 0707248_01.SLDPRT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]
2018-02-27 Add PIN functions
    [controller.sch]
2018-02-27 Stepper pulse output description
    [controller.sch]
2018-02-28 Generate firmware project with STM32CubeMX
2018-02-28 Update slide holder
    [edm_machine.SLDASM, slide_bar_holder.SLDPRT, slide_bar_holder.STL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]
2018-03-01 Oil filter holder in progress
    [m3holder.STL, oil_filter_holder.SLDASM, oil_filter_holder.SLDPRT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]
2018-03-01 Oil filter holder update
    [edm_machine.SLDASM, oil_filter_holder.SLDASM, oil_filter_holder.SLDPRT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]
2018-03-01 Remove temporary file
    [edm_machine.SLDASM]
2018-03-06 Change C211, C212 from 0402 to 0805
    [controller.sch, edm_control_board_bom.xlsx]
2018-03-06 Change C208, C210 from 0402 to 0805
    [controller.sch, edm_control_board_bom.xlsx]
2018-03-07 Add NRST to SWD connector
    [controller.sch]
2018-03-07 Display works
    [EDM Run.cfg]
2018-03-07 Update schematics with new STM32 symbol
    [controller.sch]
2018-03-07 Print menu
2018-03-07 Time and voltage settings
2018-03-08 Change terminal name from GND to +5V
    [edm_control_board.kicad_pcb]
2018-03-09 Stepper motor control
2018-03-09 Control spark voltage
2018-03-09 Breakdown and Short circuit pins
    [connectors.sch, controller.sch, edm_connectors.sch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]
2018-03-10 Breakdown and short circuit pins mixed
    [EDM.ioc, main.h]
2018-03-10 Power board control
2018-03-12 Update CubeMX script, update indentation, add timer 9
2018-03-12 Tim9 as us delay, add printf
2018-03-13 PCB Errata
2018-03-21 Retract, water pump

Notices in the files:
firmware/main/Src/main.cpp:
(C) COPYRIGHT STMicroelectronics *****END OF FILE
